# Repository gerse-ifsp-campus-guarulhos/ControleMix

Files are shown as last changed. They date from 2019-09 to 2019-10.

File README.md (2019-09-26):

# ControleMix
Circuito universal para construção de robos autonomos ou radiocontrolado

# **Resumo**

O Controle Mix é uma placa dedicada para a construção, desenvolvimento e prototipagem de robôs autônomos ou controlado, o foco dela é para robôs voltados a competição (mas isso não impede que a mesma seja usada em outros robôs ou em outras aplicações )

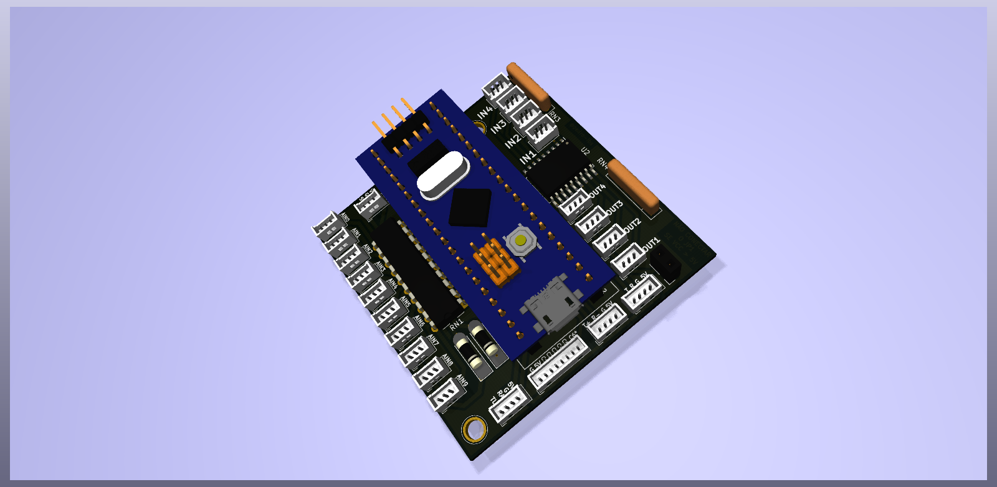
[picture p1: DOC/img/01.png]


## **Circuito**
 
O circuito leva o [STM32F103C8T6](https://www.st.com/content/ccc/resource/technical/document/reference_manual/59/b9/ba/7f/11/af/43/d5/CD00171190.pdf/files/CD00171190.pdf/jcr:content/translations/en.C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
) na plataforma  [Blue pill](https://www.techshopbd.com/uploads/product_document/STM32bluepillarduinoguide(1).pdf) a mesma dispõe de entradas e saídas e interfaces de comunicação serial , a ideia principal é universalizar os projetos e principalmente facilitar o projeto elétrico de forma que o desenvolvimento seja mais voltado para a programação. O circuito foi desenvolvido no Kicad e está projetado para fabricação manufatura ([consulte o GERBER](./DOC/GERBER/)), Para mais informações da placa consulte o [esquema elétrico](./DOC/ControleMix.pdf), O circuito contém:

* 10 entradas analogicas de 12 bits com divisor de tensão - 0V a 30V

* 4 saídas acoplada por um [ULN2803A](https://www.st.com/en/interfaces-and-transceivers/uln2803a.html)   (todas PWM)

* 4 Entradas acoplada por um  [ULN2803A](https://www.st.com/en/interfaces-and-transceivers/uln2803a.html)   (todas PWM)

* Serial USART1

* Serial USART3 / I2C2

* Serial USB / CAN

* Conector para mix de sinal do controle RF de até 6 canais

## **Notas para instalação e manipulação nos projetos:**

* sempre consulte o [esquema elétrico](./DOC/ControleMix.pdf).

* Ela tem aproximadamente 60mm por 60mm e contém 2 furos de fixação excêntrico e assimétricos.

* Aconselha se a utilizar de forma que o circuito não fique exposto, ela é utiliza  conectores [molex de passo 1.27mm](
https://www.molex.com/molex/news/display_news.jsp?channel=New&channelId=0&oid=941
)

* Os resistores do divisor de divisão de tensão e os resistores de pull up são array de resistores embora pode ser facilmente substituídos por resistores comuns

* Para desenho do projeto em [3D](./DOC/3D/) consulte o D do circuito 

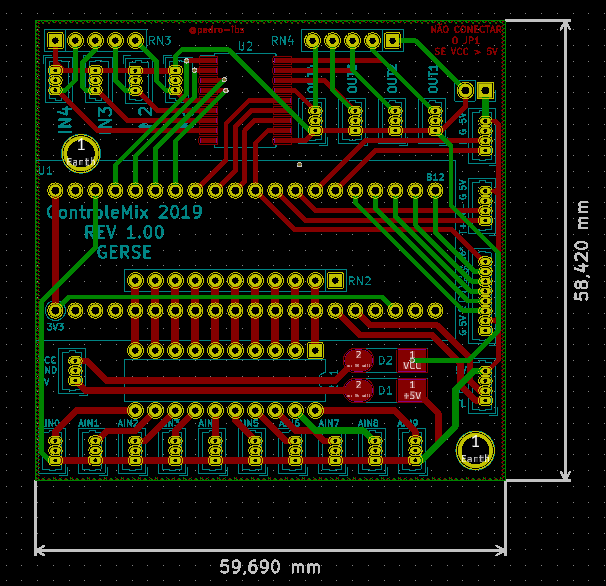
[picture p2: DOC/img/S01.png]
imagem 3d da pcb


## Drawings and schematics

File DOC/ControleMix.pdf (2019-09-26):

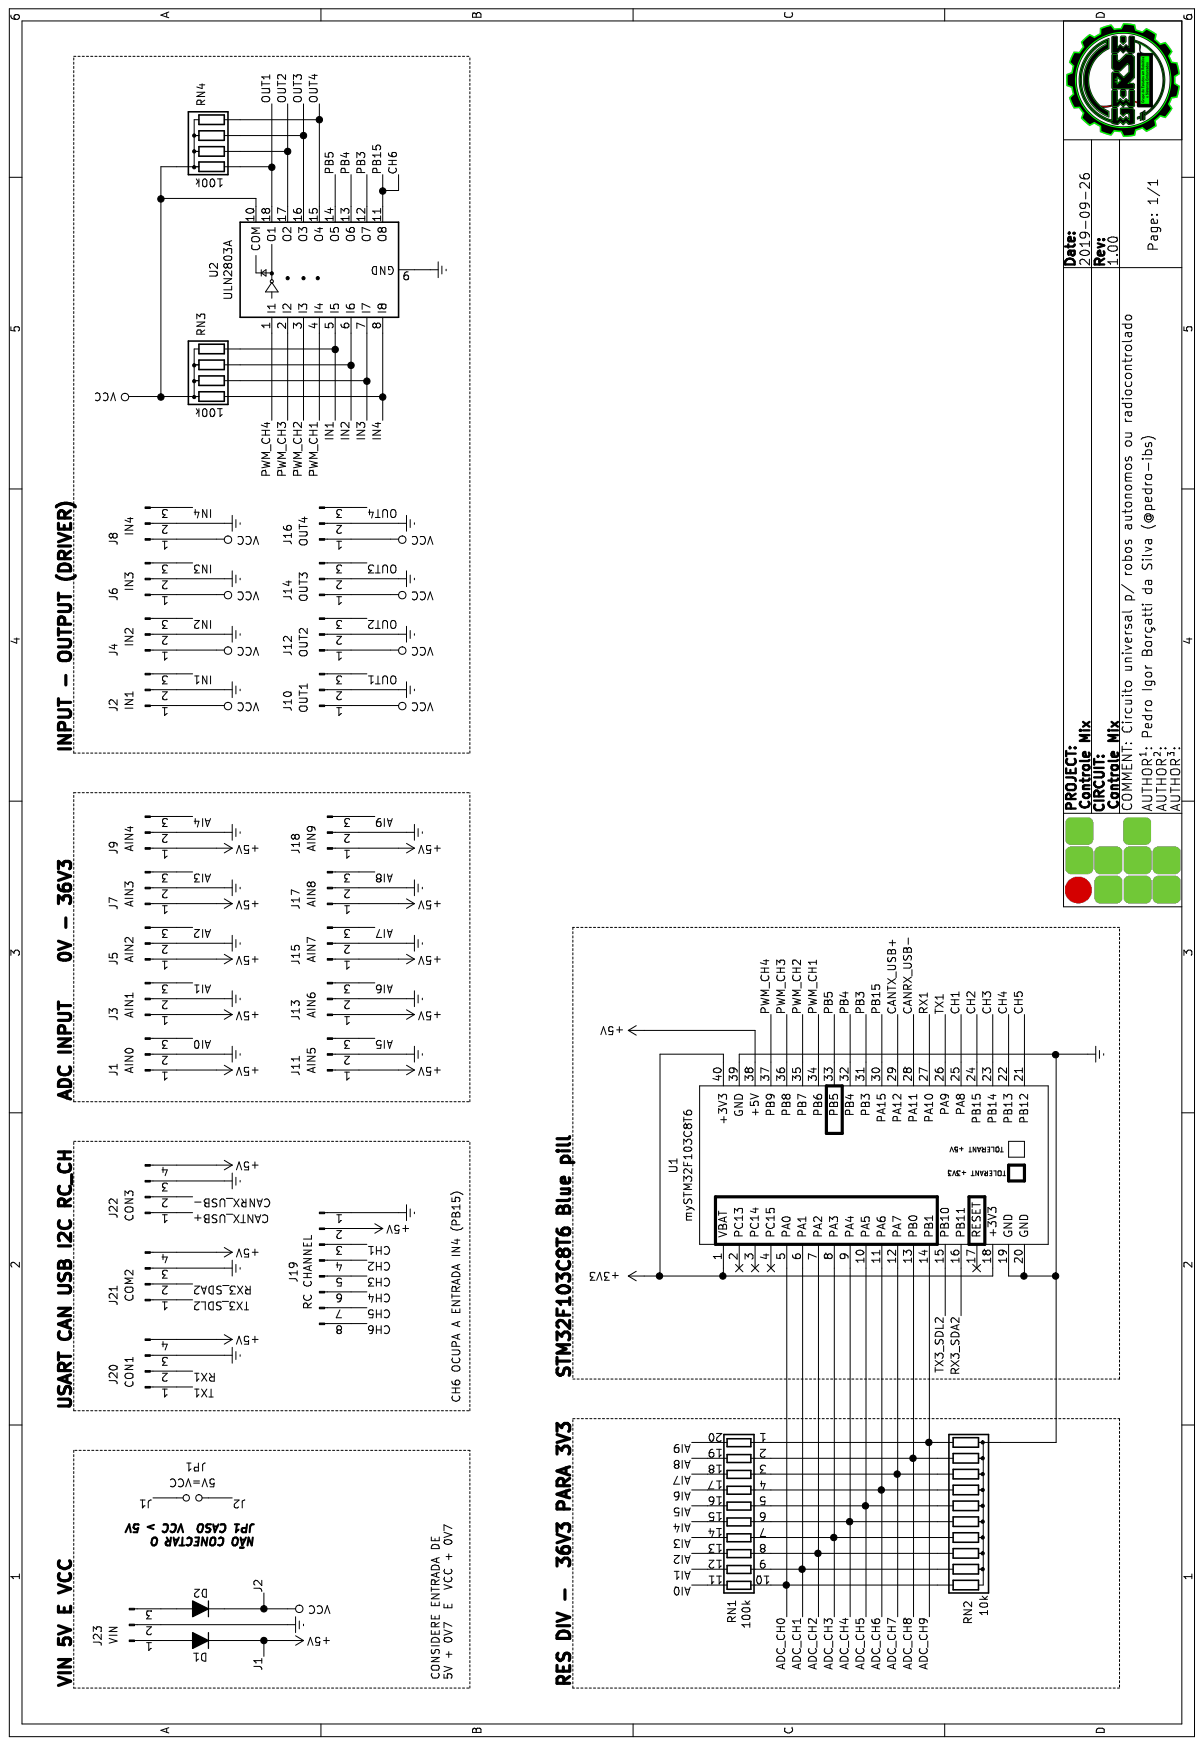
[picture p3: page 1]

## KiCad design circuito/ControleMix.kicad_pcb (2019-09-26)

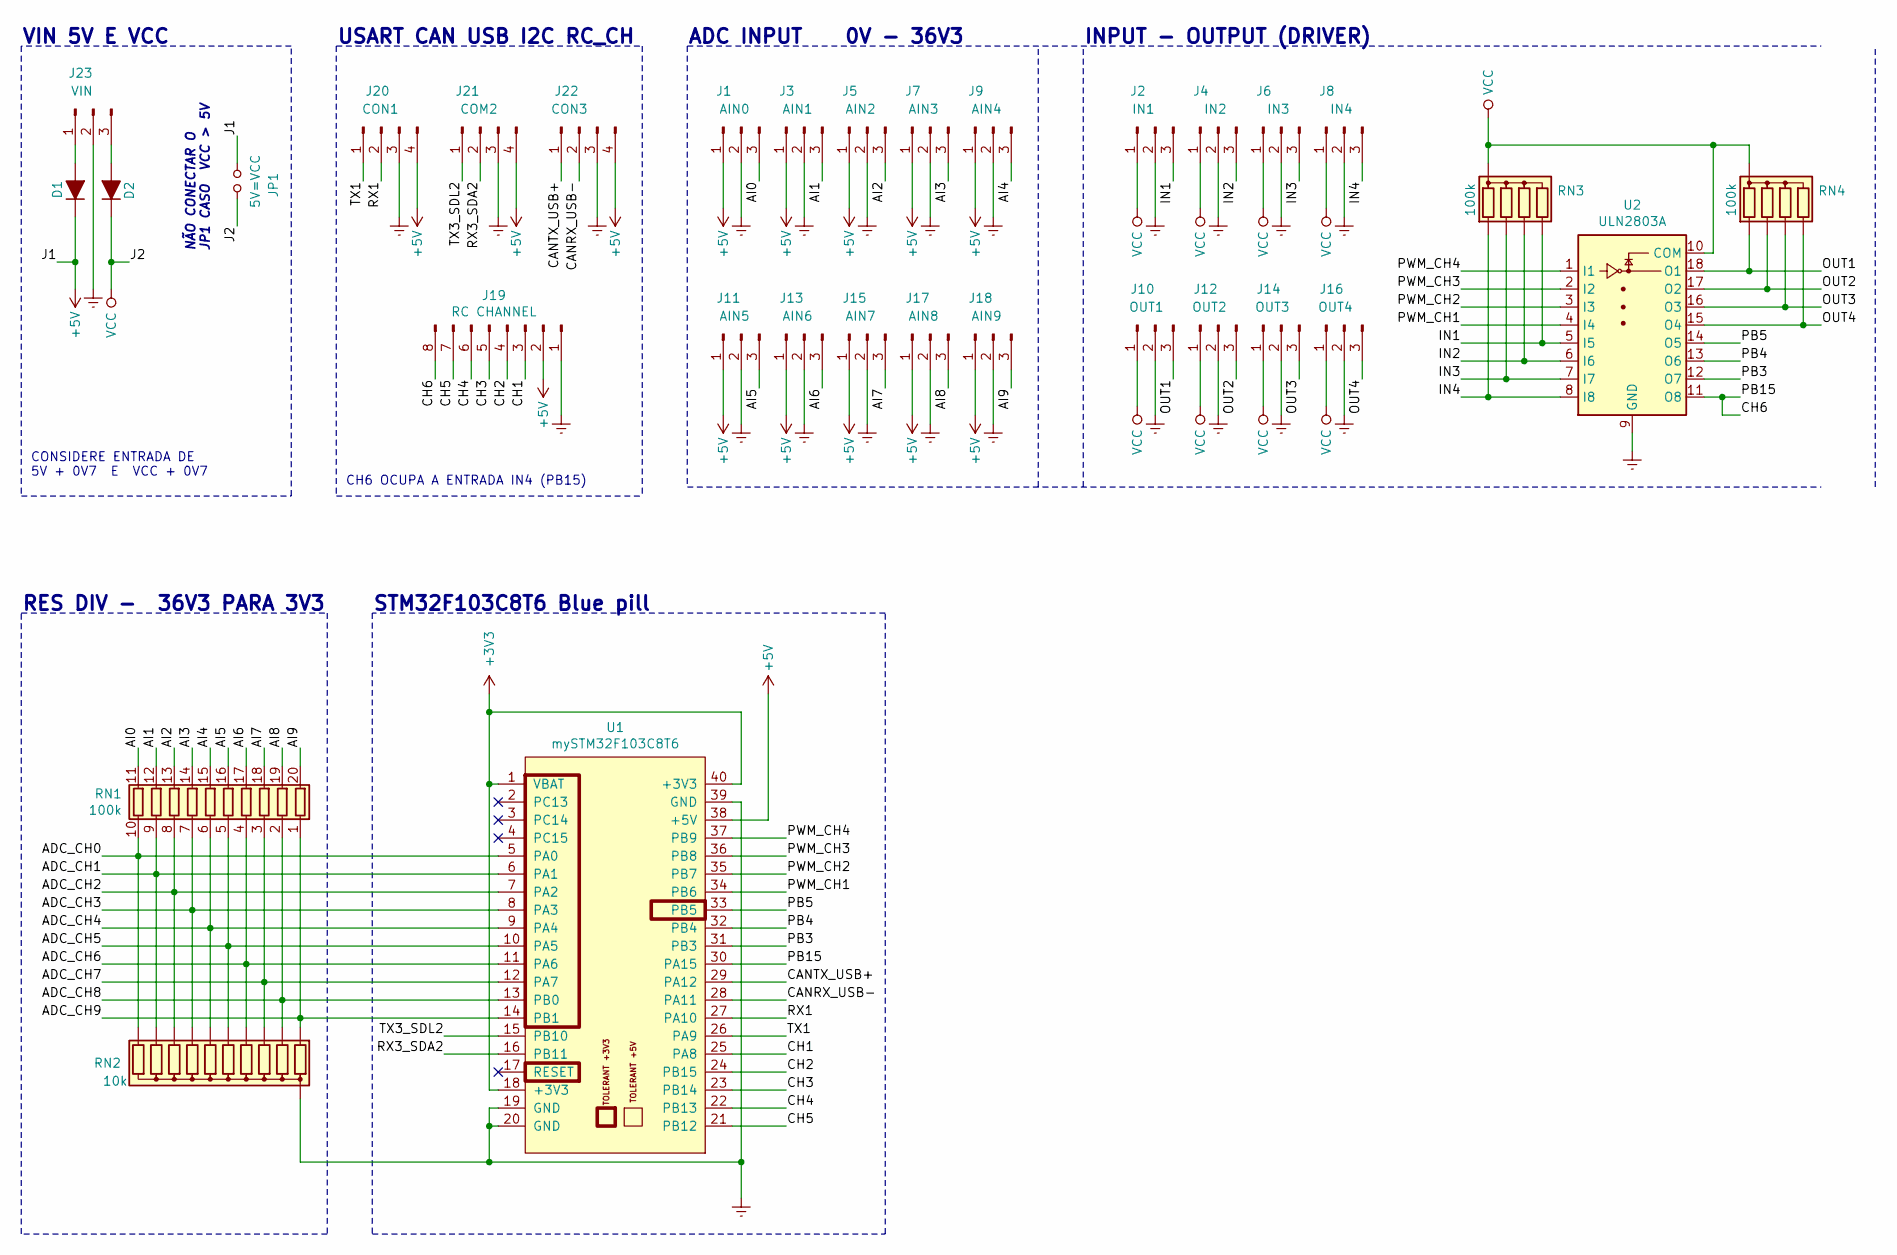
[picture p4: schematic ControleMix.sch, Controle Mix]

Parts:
D1, D2: D_ALT; D_MELF_Handsoldering
J1: AIN0; Molex_PicoBlade_53047-0310_1x03_P1.25mm_Vertical
J2: IN1; Molex_PicoBlade_53047-0310_1x03_P1.25mm_Vertical
J3: AIN1; Molex_PicoBlade_53047-0310_1x03_P1.25mm_Vertical
J4: IN2; Molex_PicoBlade_53047-0310_1x03_P1.25mm_Vertical
J5: AIN2; Molex_PicoBlade_53047-0310_1x03_P1.25mm_Vertical
J6: IN3; Molex_PicoBlade_53047-0310_1x03_P1.25mm_Vertical
J7: AIN3; Molex_PicoBlade_53047-0310_1x03_P1.25mm_Vertical
J8: IN4; Molex_PicoBlade_53047-0310_1x03_P1.25mm_Vertical
J9: AIN4; Molex_PicoBlade_53047-0310_1x03_P1.25mm_Vertical
J10: OUT1; Molex_PicoBlade_53047-0310_1x03_P1.25mm_Vertical
J11: AIN5; Molex_PicoBlade_53047-0310_1x03_P1.25mm_Vertical
J12: OUT2; Molex_PicoBlade_53047-0310_1x03_P1.25mm_Vertical
J13: AIN6; Molex_PicoBlade_53047-0310_1x03_P1.25mm_Vertical
J14: OUT3; Molex_PicoBlade_53047-0310_1x03_P1.25mm_Vertical
J15: AIN7; Molex_PicoBlade_53047-0310_1x03_P1.25mm_Vertical
J16: OUT4; Molex_PicoBlade_53047-0310_1x03_P1.25mm_Vertical
J17: AIN8; Molex_PicoBlade_53047-0310_1x03_P1.25mm_Vertical
J18: AIN9; Molex_PicoBlade_53047-0310_1x03_P1.25mm_Vertical
J19: RC CHANNEL; Molex_PicoBlade_53047-0810_1x08_P1.25mm_Vertical
J20: CON1; Molex_PicoBlade_53047-0410_1x04_P1.25mm_Vertical
J21: COM2; Molex_PicoBlade_53047-0410_1x04_P1.25mm_Vertical
J22: CON3; Molex_PicoBlade_53047-0410_1x04_P1.25mm_Vertical
J23: VIN; Molex_PicoBlade_53047-0310_1x03_P1.25mm_Vertical
JP1: 5V=VCC; PinSocket_1x02_P2.54mm_Vertical
RN1: 100k; DIP-20_W7.62mm
RN2: 10k; R_Array_SIP11
RN3, RN4: 100k; R_Array_SIP5
U1: mySTM32F103C8T6; stm32f103c8t6-module-china
U2: ULN2803A; SOIC-18W_7.5x11.6mm_P1.27mm

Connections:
+3V3: U1.1 (VBAT), U1.18 (+3V3), U1.40 (+3V3)
+5V: D1.1 (K), J1.1, J3.1, J5.1, J7.1, J9.1, J11.1, J13.1, J15.1, J17.1, J18.1, J19.2, J20.4, J21.4, J22.4, JP1.1, U1.38 (+5V)
/ADC_CH0: RN1.10 (R10.1), RN2.11 (R10), U1.5 (PA0)
/ADC_CH1: RN1.9 (R9.1), RN2.10 (R9), U1.6 (PA1)
/ADC_CH2: RN1.8 (R8.1), RN2.9 (R8), U1.7 (PA2)
/ADC_CH3: RN1.7 (R7.1), RN2.8 (R7), U1.8 (PA3)
/ADC_CH4: RN1.6 (R6.1), RN2.7 (R6), U1.9 (PA4)
/ADC_CH5: RN1.5 (R5.1), RN2.6 (R5), U1.10 (PA5)
/ADC_CH6: RN1.4 (R4.1), RN2.5 (R4), U1.11 (PA6)
/ADC_CH7: RN1.3 (R3.1), RN2.4 (R3), U1.12 (PA7)
/ADC_CH8: RN1.2 (R2.1), RN2.3 (R2), U1.13 (PB0)
/ADC_CH9: RN1.1 (R1.1), RN2.2 (R1), U1.14 (PB1)
/AI0: J1.3, RN1.11 (R10.2)
/AI1: J3.3, RN1.12 (R9.2)
/AI2: J5.3, RN1.13 (R8.2)
/AI3: J7.3, RN1.14 (R7.2)
/AI4: J9.3, RN1.15 (R6.2)
/AI5: J11.3, RN1.16 (R5.2)
/AI6: J13.3, RN1.17 (R4.2)
/AI7: J15.3, RN1.18 (R3.2)
/AI8: J17.3, RN1.19 (R2.2)
/AI9: J18.3, RN1.20 (R1.2)
/CANRX_USB-: J22.2, U1.28 (PA11)
/CANTX_USB+: J22.1, U1.29 (PA12)
/CH1: J19.3, U1.25 (PA8)
/CH2: J19.4, U1.24 (PB15)
/CH3: J19.5, U1.23 (PB14)
/CH4: J19.6, U1.22 (PB13)
/CH5: J19.7, U1.21 (PB12)
/CH6: J19.8, U1.30 (PA15), U2.11 (O8)
/IN1: J2.3, RN3.5 (R4), U2.5 (I5)
/IN2: J4.3, RN3.4 (R3), U2.6 (I6)
/IN3: J6.3, RN3.3 (R2), U2.7 (I7)
/IN4: J8.3, RN3.2 (R1), U2.8 (I8)
/OUT1: J10.3, RN4.2 (R1), U2.18 (O1)
/OUT2: J12.3, RN4.3 (R2), U2.17 (O2)
/OUT3: J14.3, RN4.4 (R3), U2.16 (O3)
/OUT4: J16.3, RN4.5 (R4), U2.15 (O4)
/PB3: U1.31 (PB3), U2.12 (O7)
/PB4: U1.32 (PB4), U2.13 (O6)
/PB5: U1.33 (PB5), U2.14 (O5)
/PWM_CH1: U1.34 (PB6), U2.4 (I4)
/PWM_CH2: U1.35 (PB7), U2.3 (I3)
/PWM_CH3: U1.36 (PB8), U2.2 (I2)
/PWM_CH4: U1.37 (PB9), U2.1 (I1)
/RX1: J20.2, U1.27 (PA10)
/RX3_SDA2: J21.2, U1.16 (PB11)
/TX1: J20.1, U1.26 (PA9)
/TX3_SDL2: J21.1, U1.15 (PB10)
Earth: J1.2, J2.2, J3.2, J4.2, J5.2, J6.2, J7.2, J8.2, J9.2, J10.2, J11.2, J12.2, J13.2, J14.2, J15.2, J16.2, J17.2, J18.2, J19.1, J20.3, J21.3, J22.3, J23.2, RN2.1 (common), U1.19 (GND), U1.20 (GND), U1.39 (GND), U2.9 (GND)
unnamed: D1.2 (A), J23.1
unnamed: D2.2 (A), J23.3
VCC: D2.1 (K), J2.1, J4.1, J6.1, J8.1, J10.1, J12.1, J14.1, J16.1, JP1.2, RN3.1 (common), RN4.1 (common), U2.10 (COM)

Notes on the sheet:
INPUT - OUTPUT (DRIVER)
ADC INPUT 0V - 36V3
VIN 5V E VCC
NÃO CONECTAR O JP1 CASO VCC > 5V
USART CAN USB I2C RC_CH
RES DIV - 36V3 PARA 3V3
CONSIDERE ENTRADA DE 5V + 0V7 E VCC + 0V7
CH6 OCUPA A ENTRADA IN4 (PB15)
STM32F103C8T6 Blue pill

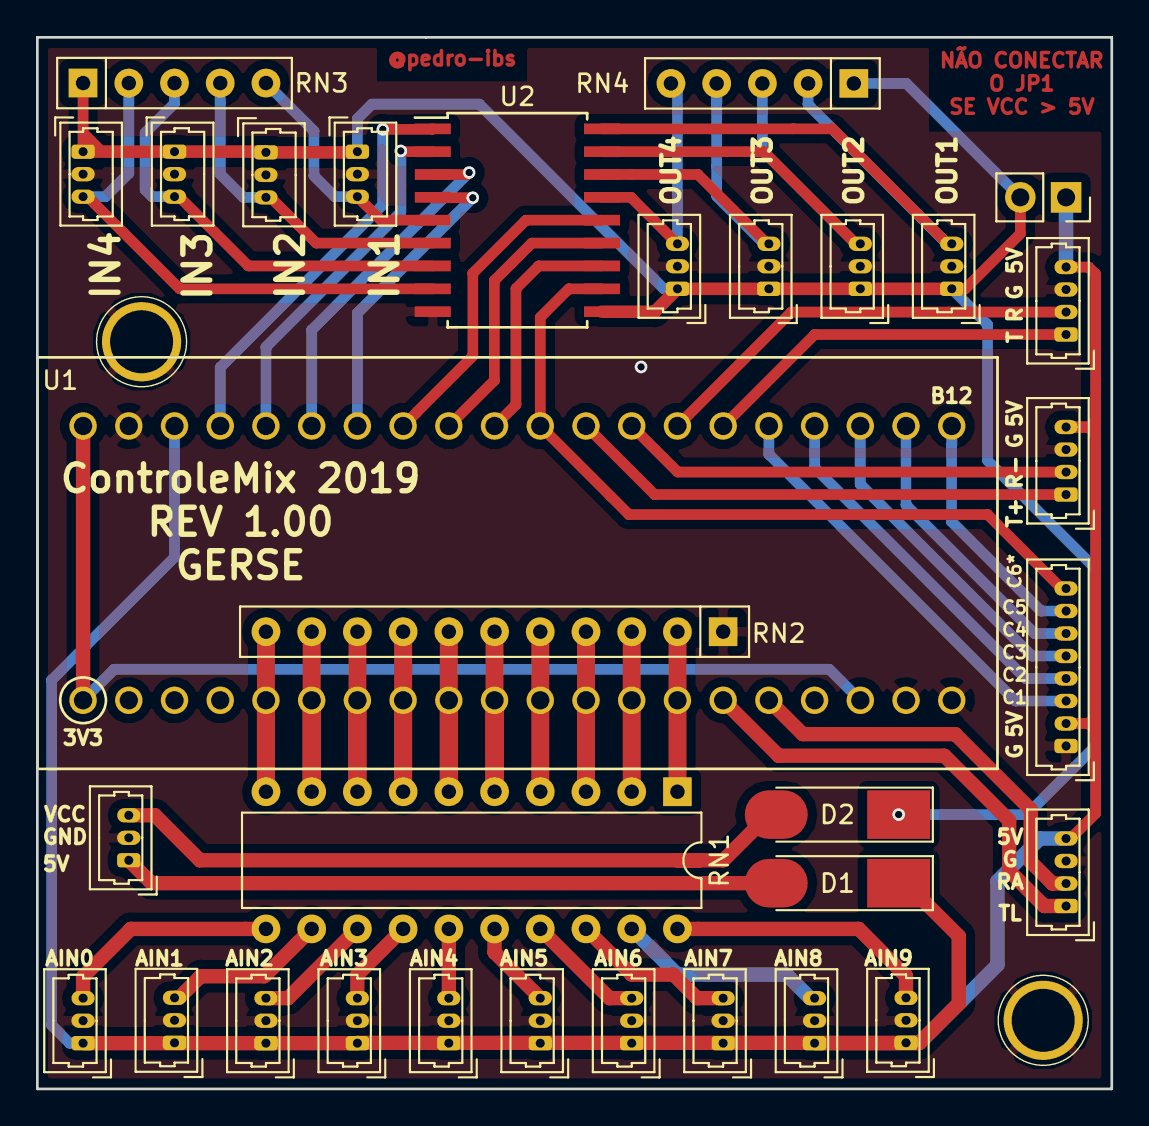
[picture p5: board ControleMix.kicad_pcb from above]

Board: 2 copper layers, 59.7 x 58.4 mm, 32 parts (0 on the bottom side), 53 nets.

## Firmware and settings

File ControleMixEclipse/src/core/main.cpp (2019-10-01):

#include <core/core.h>
#include <core/controleMix.h>

/* Private macro ---------------------------------------------------------------------------------------------------------------------------------------- */
/* Private variables ------------------------------------------------------------------------------------------------------------------------------------ */
/* Private Functions ------------------------------------------------------------------------------------------------------------------------------------ */

/* ###################################################################################################################################################### */
/* ###################################################################################################################################################### */
/* ###################################################################################################################################################### */
/* Private Functions ------------------------------------------------------------------------------------------------------------------------------------ */

/*******************************************************************************
 * tradus o programa para o formato arduino
*******************************************************************************/
int main(void){
	coreInit();	setUp();			// setup - config
	do{ blkLed();	loop(); coreMonitor(); }while(true); 	// loop principal
	return 0;
}

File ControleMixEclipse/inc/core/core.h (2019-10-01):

/*
 * config.h
 *
 *  Created on: 27 de set de 2019
 *      Author: pibs
 */

#include <sysBase/gpio.h>
#include <sysBase/pwm.h>
#include <sysBase/adc.h>
#include <sysBase/usartx.h>
#include <core/protocol.h>
#include <core/dbg.h>
#include <core/chMix.h>


#ifndef CONFIG_H_
#define CONFIG_H_

// config da comunicação serial e DBG
#define DEC			10		// base 10, conversão str -> int do dbg
#define BAUDRATE		19200		// velocidade
#define USART_DBG		USART1		// periferio
#define SERIAL			USART_DBG	// tradução


// config de inicialização do timer e rtc
#define MINIMAL_TIME_MS		1		// tempo minimo do millis()
#define INIT_CONTER		0		// iniciar contagem do milles em zero

// lede do pill blue
#define LED			GPIOC13		//
#define TIME_BLK		200		// tempo em miles segundos para piscadas do les 13


// entrada drvere
#define IN1 			GPIOB5
#define IN2 			GPIOB4
#define IN3 			GPIOB3
#define IN4 			GPIOA15		// TB É CH6

// saidas driver e PWM
#define OUT1 			PWM_CH4
#define OUT2 			PWM_CH3
#define OUT3 			PWM_CH2
#define OUT4 			PWM_CH1

// adc
#define AIN0			ADC_CH0
#define AIN1			ADC_CH1
#define AIN2			ADC_CH2
#define AIN3			ADC_CH3
#define AIN4			ADC_CH4
#define AIN5			ADC_CH5
#define AIN6			ADC_CH6
#define AIN7			ADC_CH7
#define AIN8			ADC_CH8
#define AIN9			ADC_CH9

// entrada do controle RS
#define CH1			GPIOA8
#define CH2			GPIOB15
#define CH3			GPIOB14
#define CH4			GPIOB13
#define CH5			GPIOB12
#define CH6			GPIOA15		// TB É IN4


void coreInit(void);
void blkLed(void);
void coreMonitor(void);
bool initIsOK(void);

#endif /* CONFIG_H_ */

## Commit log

2019-09-26 new rep fcm
    [ControleMix-B.Cu.gbr, ControleMix-B.Mask.gbr, ControleMix-B.Paste.gbr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]
2019-09-26 arrumando esquema
    [ControleMix.sch]
